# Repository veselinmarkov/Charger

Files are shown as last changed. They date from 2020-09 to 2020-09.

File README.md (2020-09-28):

# Charger
High power electric car charger

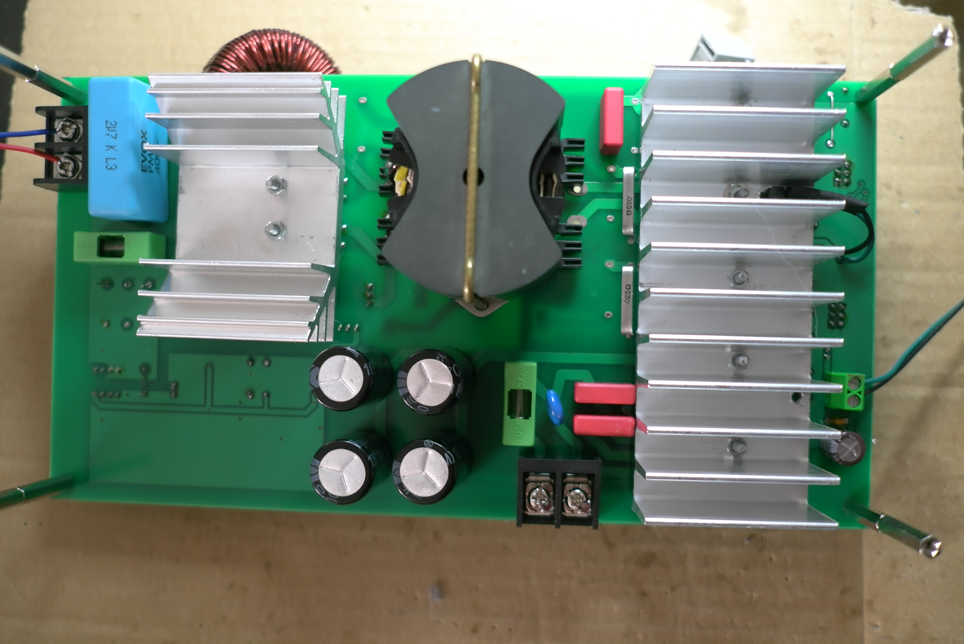
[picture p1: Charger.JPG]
Prototype board Prototype Board


The AC-DC charger was designed as part of an electric car project. 
The planned power is up to 3KW for charging 160V - 200V car batteries at nominal current of 10A, 15A at maximum. The switching frequency is 100kHz.
Apart from the core switching circuit there are some additional modules implemented, like input/output voltage measurement, overcurrent switch transistor protection, switching transistors temperature protection, CAN communication 

In the current state of the project the prototype is built, all the modules are tested and are working properly, except CAN. 
There are some topics that must be improved in to-do list

The detailed description and the first tests are collected in the Charger description document.

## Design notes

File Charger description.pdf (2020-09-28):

## Battery charger description

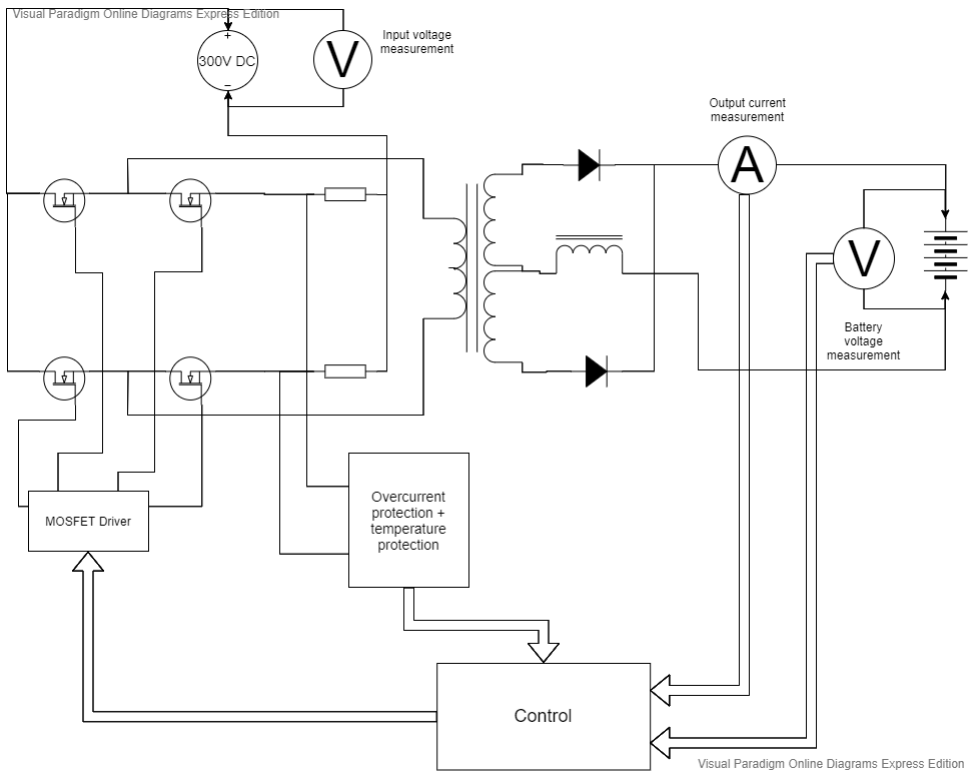
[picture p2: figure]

The charger is powered by the single phase 220V source and after rectification and filtering the DC voltage is approximately 300V. The filter capacitors need not to be large, since some pulsation is tolerable when charging batteries.

The switching type is full bridge, using phase shift technique. Both parts of the bridge are fed with fixed 50% duty cycle pulse train. The phase shift between the half bridges controls the output current. The MOSFET drive signals, current feedback and the UART control are managed by dsPIC33FJ16GS502 microcontroller. It is a special purpose PIC series for implementing in DC-DC conversions up to 400кHz.

### Switching circuit

The switching transistors are SPW17N80C3 in TO247 package. The maximum ratings are 17A drain current and 800V drain-source voltage. During the switching off phase It is highly possible to have 600V DC voltage at the transistors.

### Transformer

The transformer uses Epcos PM62/49 B65684A0000R027 ferrite N27 cores. The cores could be purchased with the matching coil former. The ratio is 12:10:10 windings with 3mm copper wire. The secondary winding is center tapped.
The transformer ratio could be changed in accordance with the battery voltage. In that case the output voltage control must be corrected in the software.

### Rectifiers

The full wave rectifier uses 2 diodes of type DSEP29-12A It is Fast Diode, 1.2 kV, 30 A, 40 ns. Have in mind that

the double voltage is applied over the reverse polarized diode in the full wave rectifier. That is why we should pick at least 1.2kV diode. It must be also soft recovery diode to decrease the switching spikes in the secondary circuit.

Filter inductor is used to limit the current in the output. I chose Epcos B66387G0000X187 ferrite with 70 wounds of 2mm wire. 1mm gap in the ferrite is required to prevent saturation at 10A charging current.

### Overcurrent and temperature protection

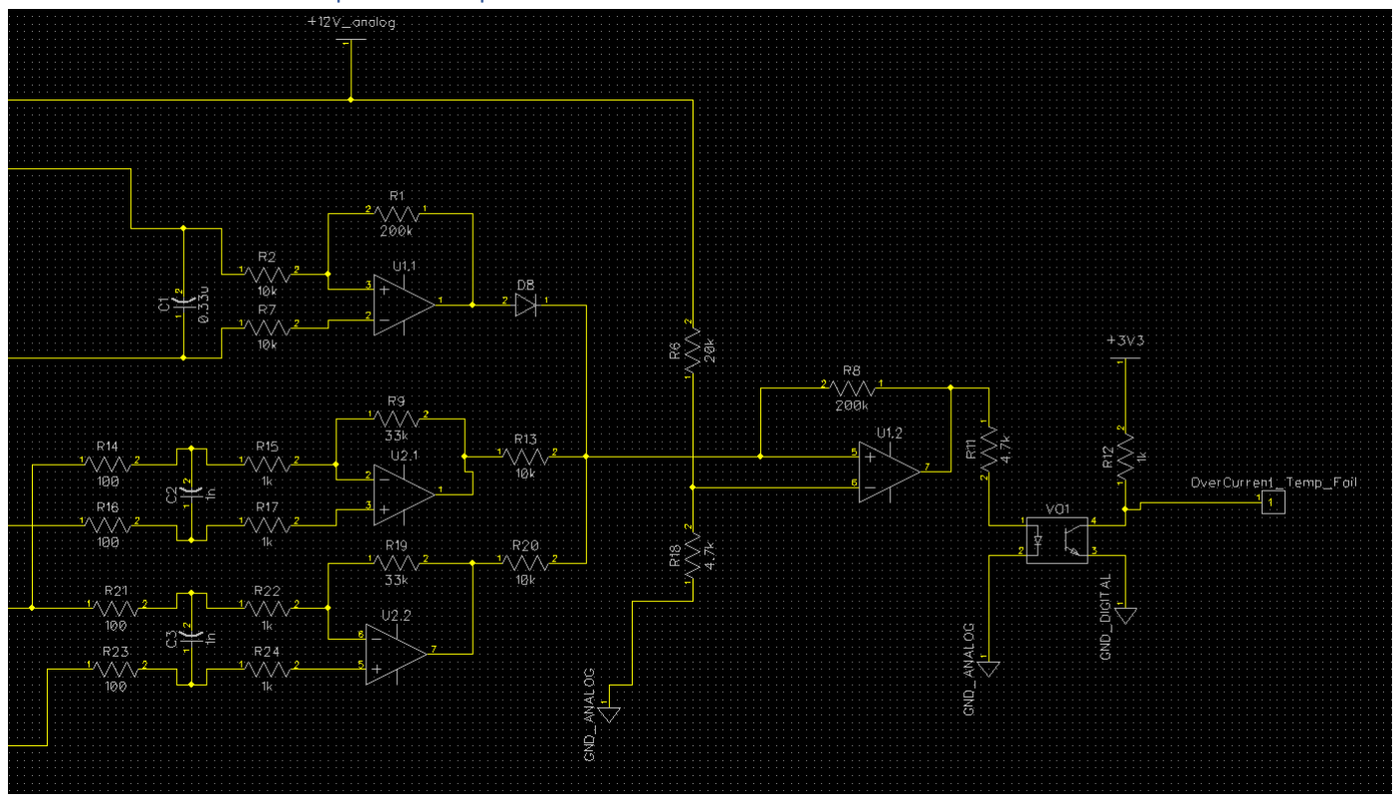
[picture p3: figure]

The overcurrent protection is accomplished of 2 shunts R1 and R2, on each leg of the bridge. After filtering the current signal is applied to the differential amplifiers U2.1 and U2.2. Adding both amplified signals goes to the comparator U1.2. In case the current via switching transistors increases above 8-9A, the overcurrent signal is triggered at pin AN2/RA2 of the PIC. The microcontroller fail-signal switches off the PWM generator. After the overcurrent condition subside, the PWM generator resumes it’s function.

The thermo protection is accomplished by a thermistor TDK B59901D0060A040. It is not shown on the circuit diagram, but the thermistor is connected to pin J3-6 and is part of the resistor bridge R3-R4-R10. Tested at 60 deg the thermistor reaches 10kOm and triggers the comparator U1.1. Via the diode D8 the thermo protection is applied to the same fail pin of the PIC microcontroller.

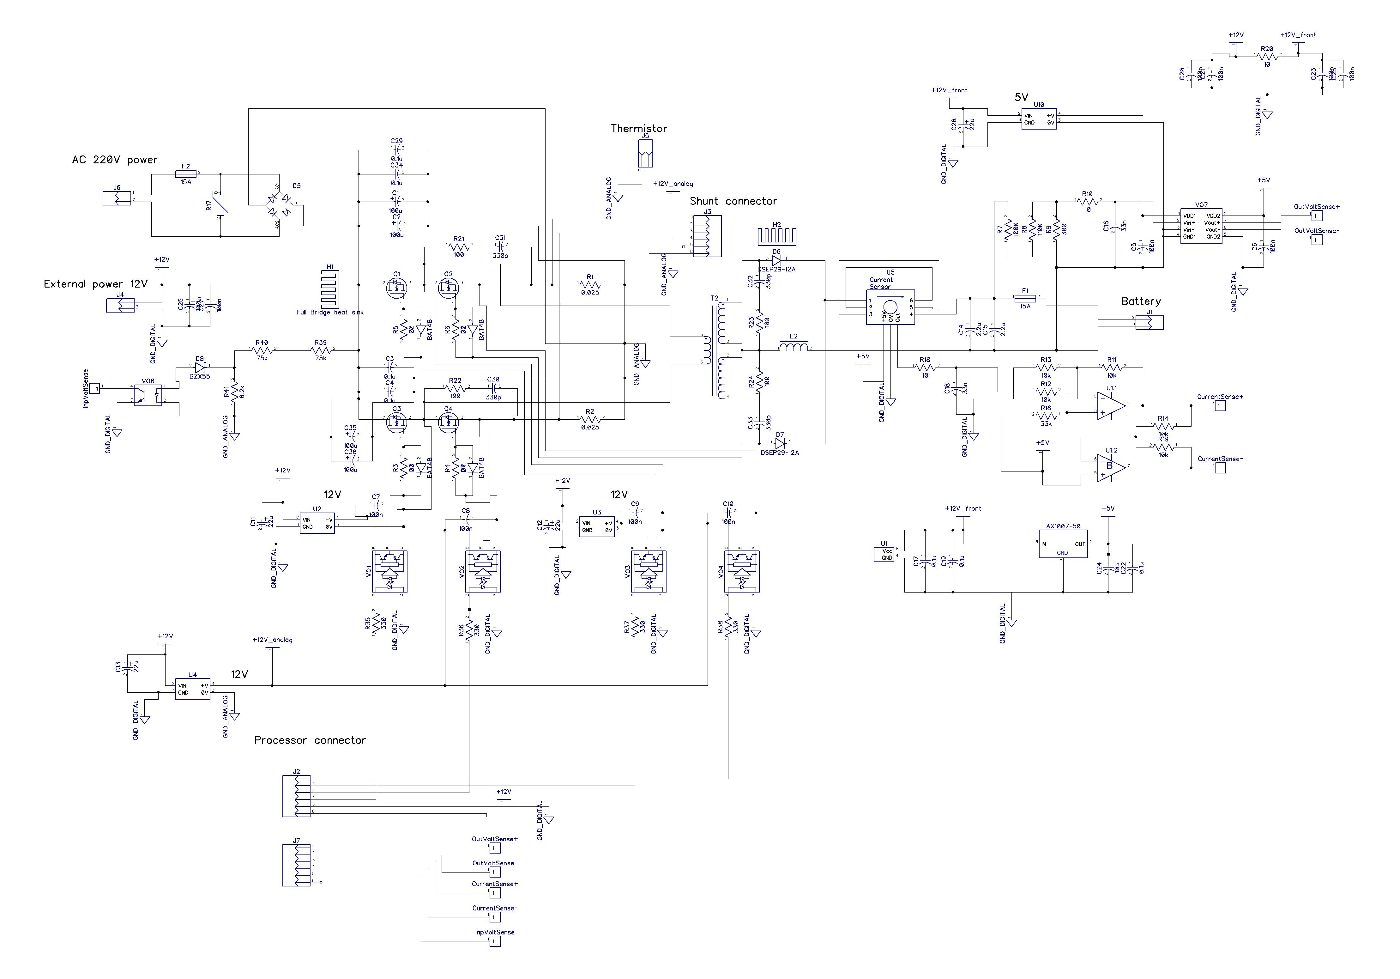
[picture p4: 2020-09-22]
Main_board_schematic.jpg

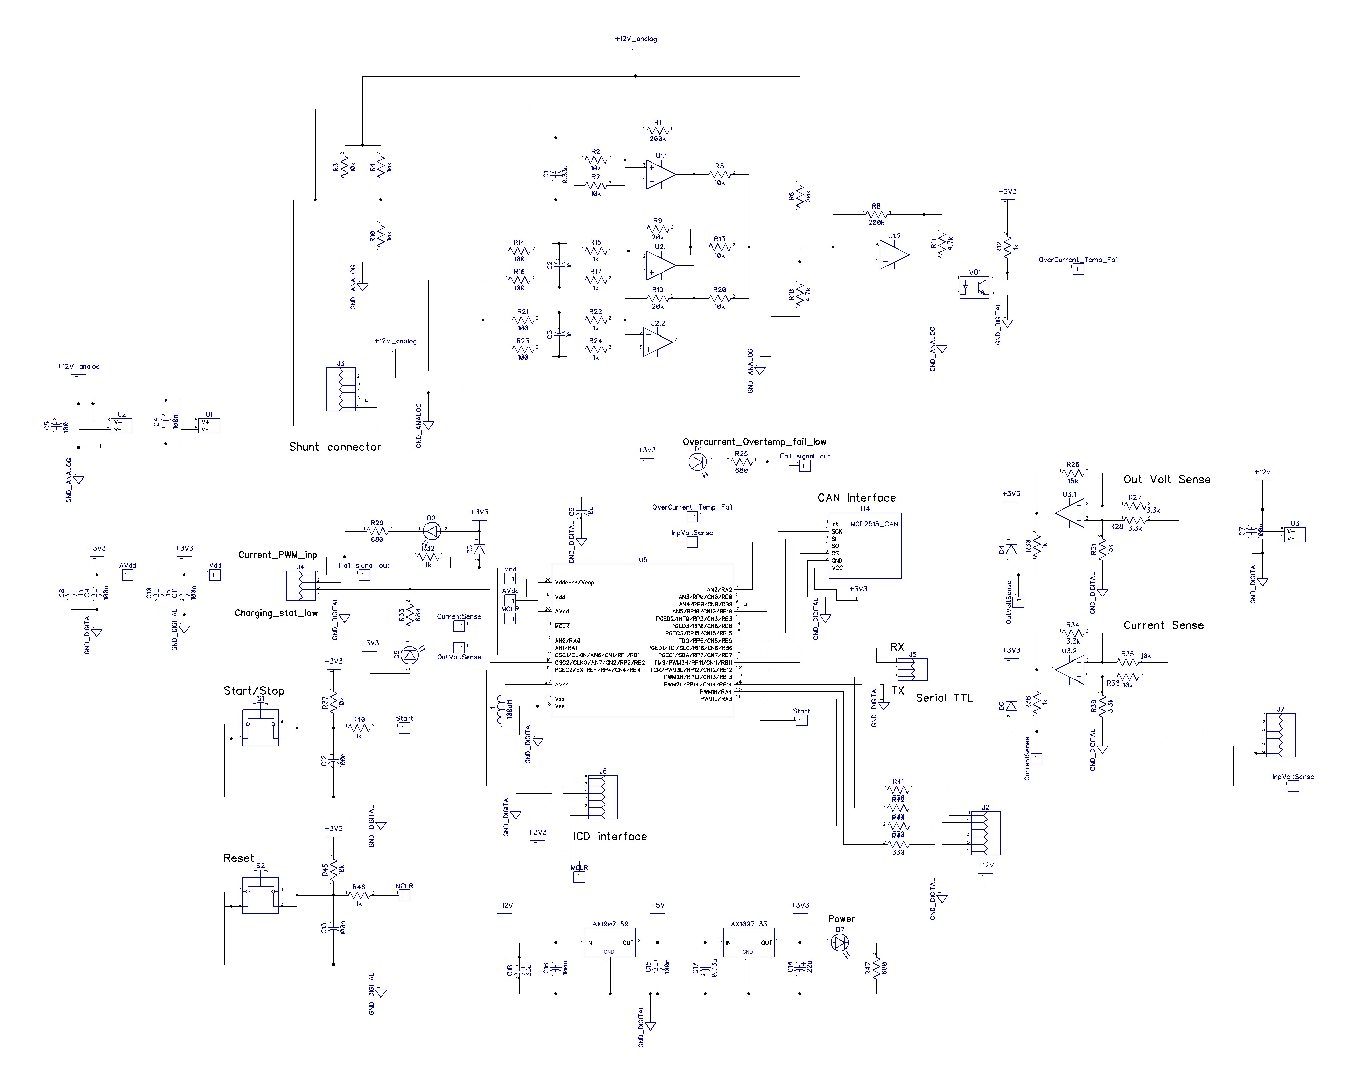
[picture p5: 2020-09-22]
Control_board_schematic.jpg

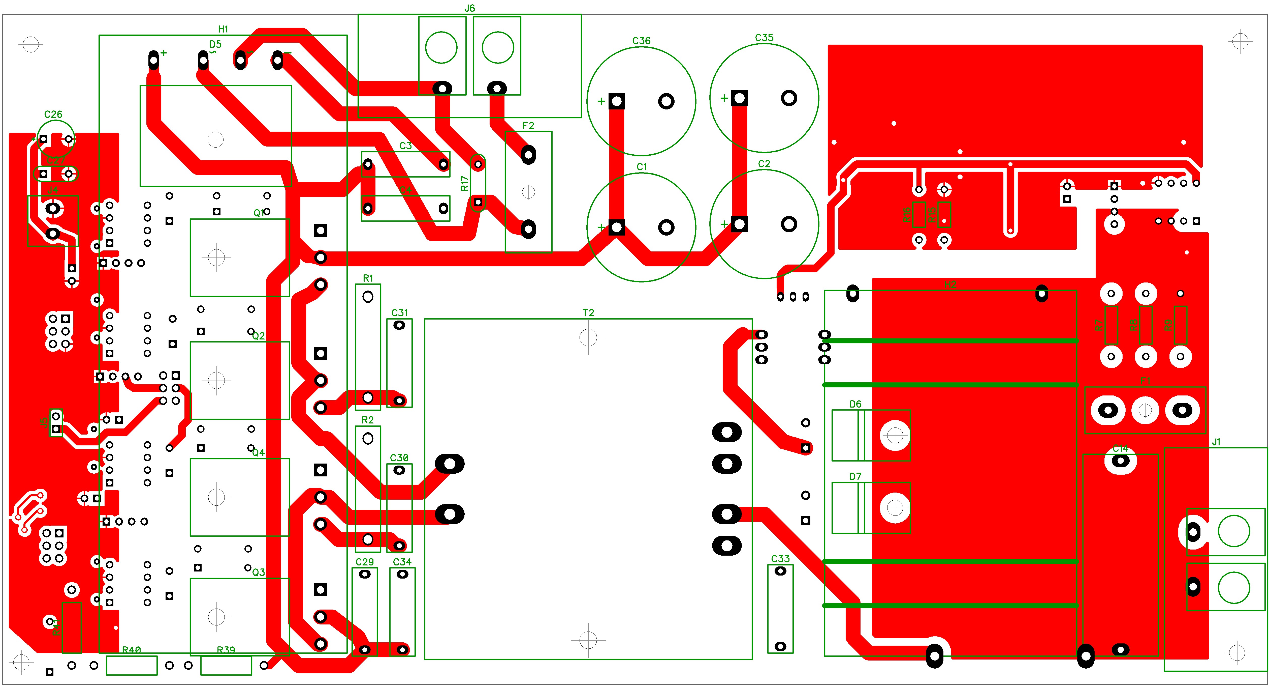
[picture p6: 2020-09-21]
pcb/Main_board_side_1.jpg

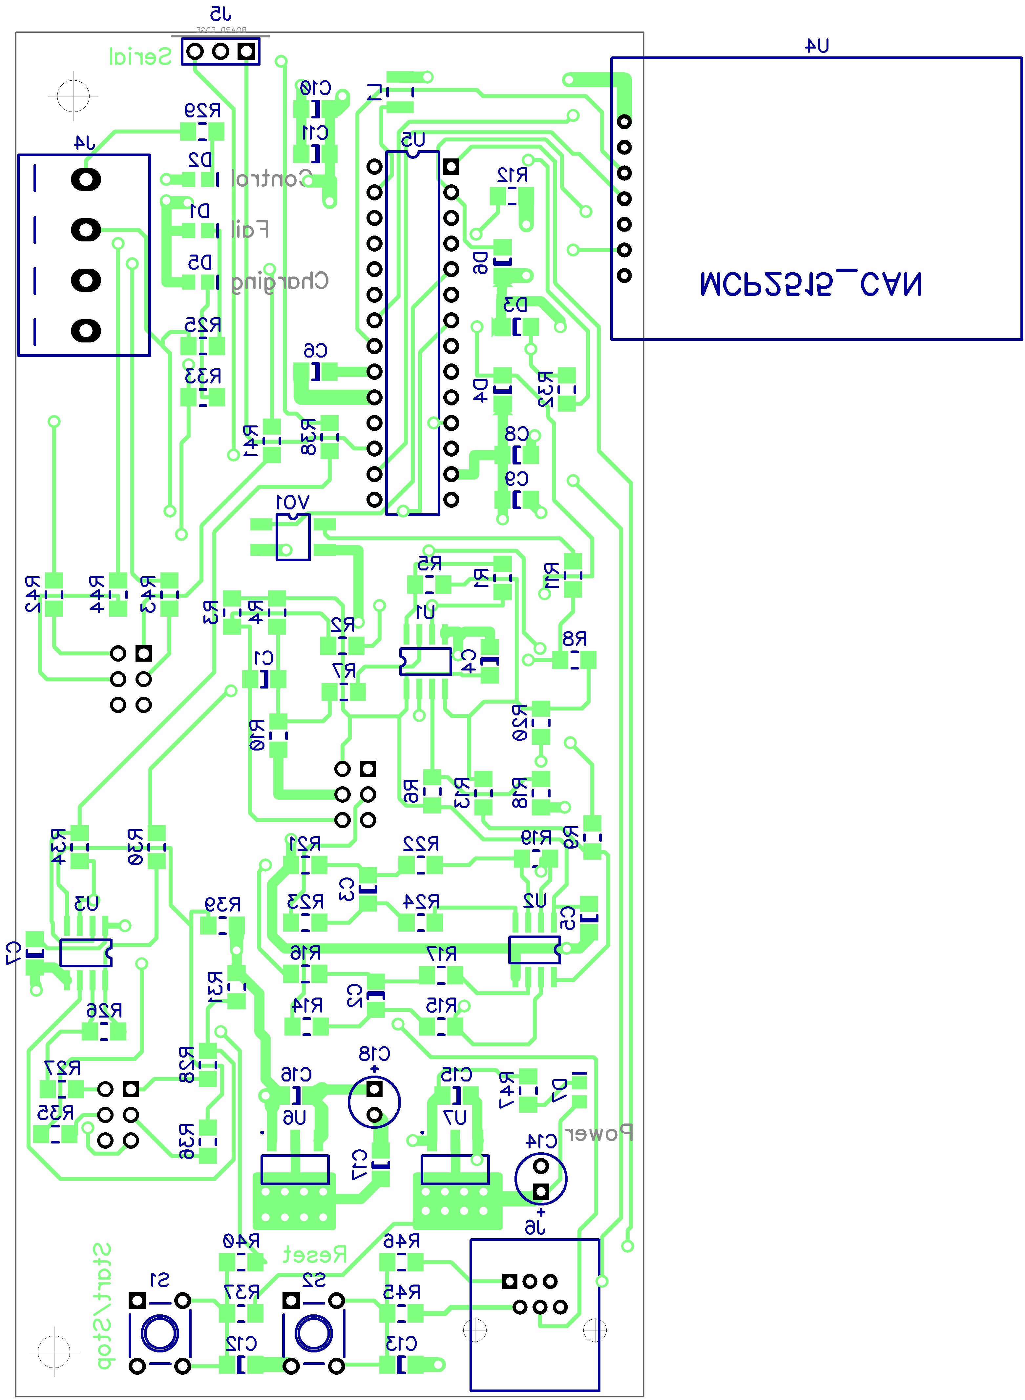
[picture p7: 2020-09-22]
pcb/Control_board_side_2.jpg

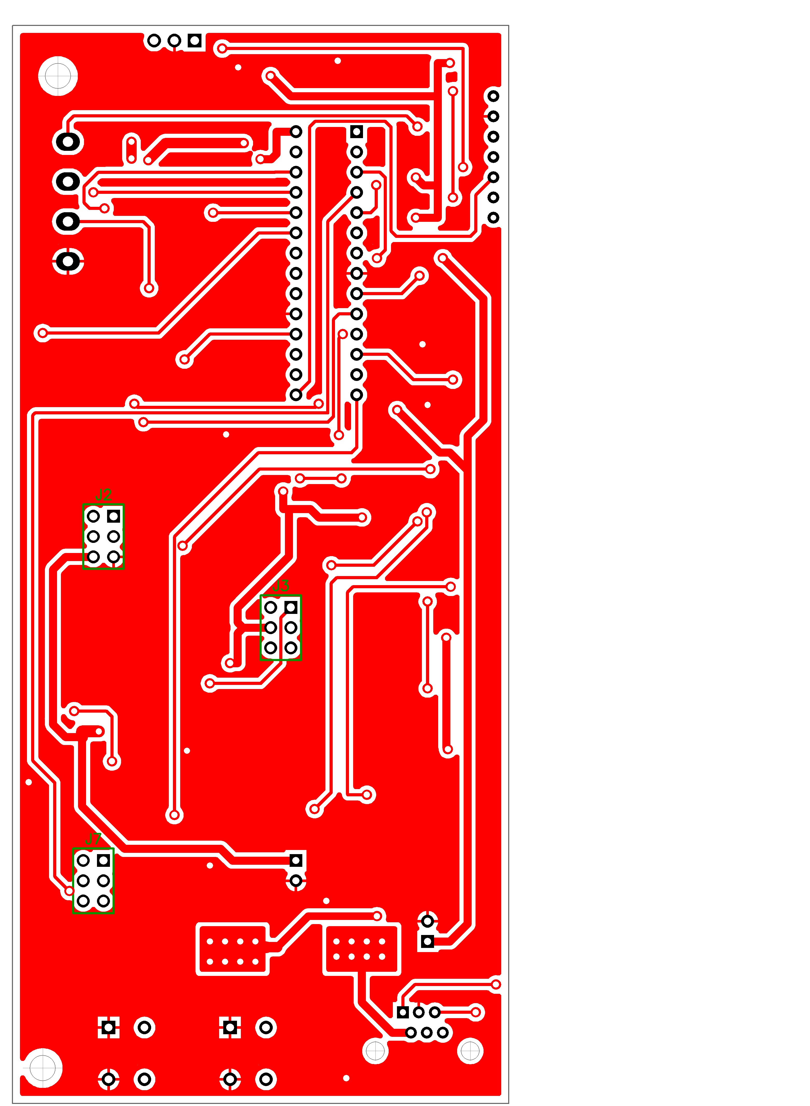
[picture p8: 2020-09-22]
pcb/Control_board_side_1.jpg

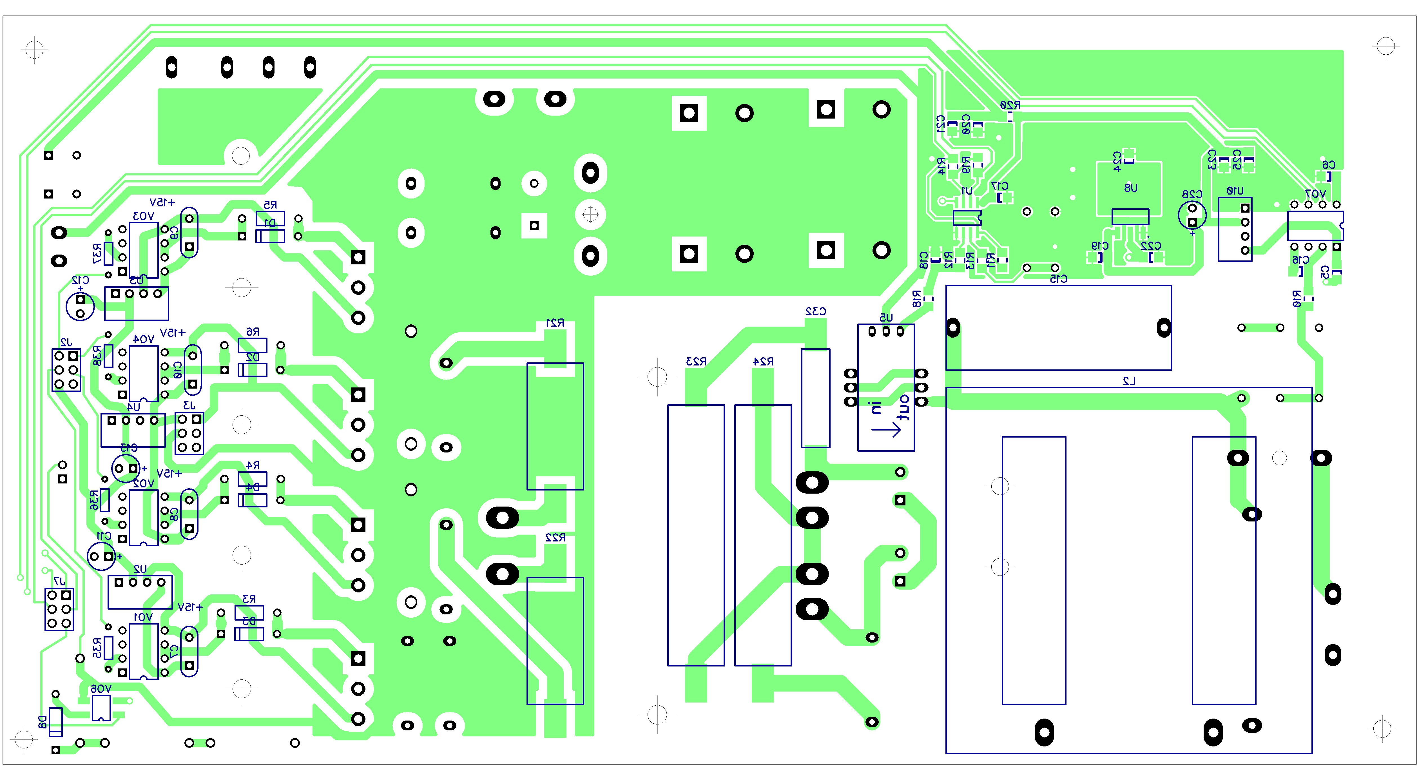
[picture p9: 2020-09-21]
pcb/Main_board_side_2.jpg

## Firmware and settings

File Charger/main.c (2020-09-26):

//Microchip example PID function is used. See their License in "pid.s" source code. The PID structure is defined in dsp.h


#include "p33FJ16GS502.h"
#include "Functions.h"
#include "CAN_transmit.h"
#include "string.h"
#include "stdio.h"
#include "stdlib.h"

_FOSCSEL(FNOSC_FRC)
_FOSC(FCKSM_CSECMD & OSCIOFNC_ON)
_FWDT(FWDTEN_OFF)
_FPOR(FPWRT_PWR128)
_FICD(ICS_PGD2 & JTAGEN_OFF)

#define OutputChargeFinish 784                                  // Not implemented: Defones voltage limit to switch off the charging

#define OutputBatteryPresent 280                                // Not implemented: Minimal voltage to detect if the battery is conncted

// extern tPID Buck1VoltagePID;
extern int zero_transducer, average, vout_average;
double AlphaOutVolt =0.0278, BetaOutVolt = 0.0;   //Alpha and Beta coefficients in the equation OutVolt =Alpha*steps +Beta for the out voltage
int PotVoltage, CurrentTarget, OutVolt1, OutVolt1steps, InVoltage, n;
char UART_logger_interval = -1;        //Return pressed via UART; if -1 the logger is switched off
extern char UART_CR;
extern char UART_buff[16];
char UART_logger_buff[150];
int PID_enable =0;
char CAN_result;

double StepToFloat(int current) {
    //return (double)0.01052*current; //95 steps per amper
    return (double)1.0 * current;
}

//current state Vout measure: R7+R8 = 3.29kOm; R9 = 33 Om; gain =1/100; max input = 30V
//              In volt=5mV; in ACPL-7900 = 1mV; out ACPL = 7mV; ADC AN1 = 50mV (noise); steps=14  
//              In volt=4.09V; in ACPL-7900 = 42mV; out ACPL = 104mV; ADC AN1 = 490mV (amp=4.54); steps =147; alpha = 0.0278
double returnOutVolt(int voltage) {
    return (double)AlphaOutVolt*voltage +BetaOutVolt;
}

void measureIdleCurrent(void) {  // PWM must be switched off before invoke
    ADCONbits.ADON = 0;
    Delay_ms(100);                                        //wait some time to measure zero current offset
    ADSTATbits.P0RDY = 0; 				  /* Clear Pair 0 data ready bit */
    ADCPC0bits.TRGSRC0 = 1;                               /* ADC Pair 0 triggered by soft trigger */
    ADCONbits.ADON = 1;                                   //enable temporary the ADC
    ADCPC0bits.SWTRG0 =1;                                 // new sample for pair 0
    while (ADSTATbits.P0RDY == 0);                         // wait to finish the zero measurement
    zero_transducer = ADCBUF0;
    ADCPC0bits.TRGSRC0 = 4; 			  /* ADC Pair 0 triggered by PWM1 */
    ADCONbits.ADON = 1;
}

int measureInputVolt(void) {
    ADSTATbits.P1RDY = 0;						// Clear the ADC pair 1 ready bit
    ADCPC0bits.SWTRG1 =1;                       // new sample for pair 1
    while (ADSTATbits.P1RDY == 0);                         // wait to finish the zero measurement
    return ADCBUF2;
 }

// Pins definitions
//Current Buck1 - AN0/RA0 (pin2) = FB0 
//Volt Buck1 out - AN1/RA1 (pin3) = FB1
//Volt Buck1 in - AN2 (pin4) = FB4
//Over current/over temp signal in - AN3/RP0/RB0 (pin5)
//Over current/over temp status active low out - AN5/RB10 (pin7)
//Charging status active low out- AN7/RB2 (pin10)
//Charging current 0-100% external drive PWM signal in - AN6/RB1 (pin9)  
//start/stop switch in - RB8/RP8 (pin14)
//SPI signals: CS - RP11 (pin21); SCK - RP12 (pin22); SI - RP5 (pin16); SO - RP15 (pin15)
//UART new: TX - RP7 (pin18) RX - RP6 (pin17)
int main(void)
{
	
	/* Configure Oscillator to operate the device at 40Mhz
	   Fosc= Fin*M/(N1*N2), Fcy=Fosc/2
 	   Fosc= 7.37*(43)/(2*2)=80Mhz for Fosc, Fcy = 40Mhz */

	/* Configure PLL prescaler, PLL postscaler, PLL divisor */
	PLLFBD = 41; 							/* M = PLLFBD + 2 */
	CLKDIVbits.PLLPOST = 0;   				/* N1 = 2 */
	CLKDIVbits.PLLPRE = 0;    				/* N2 = 2 */

    //remappable inputs
    RPINR29bits.FLT1R =0;                   // RP0/RB0 is PWM fault/current source
    TRISBbits.TRISB0 =1;                    //config RB0(RP0) as an input
    ADPCFGbits.PCFG3 =1;                    //config RP0 = AN3 AS DIGITAL/NOT ANALOG
    RPINR20bits.SDI1R =5;                   // Pin RP5 SPI:SI
    TRISBbits.TRISB5 =1;                    //config RB5(RP5) as an input
    RPINR18bits.U1RXR = 6;			// Make Pin RP6 U1RX
    TRISBbits.TRISB6 =1;                    //config RB6(RP6) as an input
    //RPINR20bits.SCK1R =12;
    //RPINR21bits.SS1R =11;
    
    //remappable outputs
    RPOR7bits.RP15R = 0b000111;  //SDO
    RPOR6bits.RP12R = 0b001000; //SCK
    RPOR5bits.RP11R = 0b001001; //CS
	RPOR3bits.RP7R = 3;		// Make Pin RB7 (RP7) U1TX
//	RPOR4bits.RP9R = 3;		// Make Pin RB9 (RP9) U1TX
    TRISBbits.TRISB15 =0;
    TRISBbits.TRISB12 =0;
    TRISBbits.TRISB11 =0;
    TRISBbits.TRISB10 =0;           //Digital out fault indication signal  AN5/RB10 (pin7)
    ADPCFGbits.PCFG5 =1;            //config  AN5/RB10 (pin7) AS DIGITAL/NOT ANALOG
    LATBbits.LATB10 =1;             //switch if off
    TRISBbits.TRISB2 =0;           //Digital out signal charging indication AN7/RB2 (pin10)
    ADPCFGbits.PCFG7 =1;            //config AN7/RB2 (pin10) AS DIGITAL/NOT ANALOG
    LATBbits.LATB2 =1;             //switch if off             

    __builtin_write_OSCCONH(0x01);			/* New Oscillator selection FRC w/ PLL */
    __builtin_write_OSCCONL(0x01);  		/* Enable Switch */
      
	while(OSCCONbits.COSC != 0b001);		/* Wait for Oscillator to switch to FRC w/ PLL */  
        while(OSCCONbits.LOCK != 1);			/* Wait for Pll to Lock */

	/* Now setup the ADC and PWM clock for 120MHz
	   ((FRC * 16) / APSTSCLR ) = (7.37MHz * 16) / 1 = 117.9MHz*/
	
	ACLKCONbits.FRCSEL = 1;					/* FRC provides input for Auxiliary PLL (x16) */
	ACLKCONbits.SELACLK = 1;				/* Auxiliary Ocillator provides clock source for PWM & ADC */
	ACLKCONbits.APSTSCLR = 7;				/* Divide Auxiliary clock by 1 */
	ACLKCONbits.ENAPLL = 1;					/* Enable Auxiliary PLL */
	
	while(ACLKCONbits.APLLCK != 1);			/* Wait for Auxiliary PLL to Lock */

    Buck1Drive();							/* PWM Setup */
        /* Complementary mode, 400kHz, dead time 25ns, ALT dt 50ns, primary timebase, disable immediate updates, trigger every cycle, fault disabled */
    CurrentandVoltageMeasurements();		/* ADC Setup */
    measureIdleCurrent();                   // Measure the Idle current and store in zero_transducer
    Buck1VoltageLoop();    					/* Initialize Buck1 PID */

    SPI_setup();
    UART_setup();
    
    IEC0bits.U1RXIE =1;                                         // Enable UART RX interrupt
    IFS0bits.U1RXIF = 0;                                        // Clear UART RX interrupt
    ADCONbits.ADON = 1;						/* Enable the ADC */
    PTCONbits.PTEN = 1;						/* Enable the PWM */
    
    //Stop the PWM
    IOCON1bits.OVRENH = 1;
    IOCON1bits.OVRENL = 1;
    IOCON2bits.OVRENH = 1;
    IOCON2bits.OVRENL = 1;

    CurrentTarget =40;              // 1Amp current target
    while(1)
    {
                    if (UART_CR ==1) {                                                       // process UART commands
                        UART_CR =0;
                        if (strncmp("ATLOGON", UART_buff, 7) ==0) {                          //start the logger
                            UART_string_out("OK");                                           
                            UART_logger_interval =0;
                        }
                        else if (strncmp("ATLOGOFF", UART_buff, 8) ==0) {                    //stop the logger                                                  // process UART commands
                            UART_string_out("OK");
                            UART_logger_interval =-1;
                        }
                        else if (strncmp("ATON", UART_buff, 4) ==0) { 
                            n =atoi(UART_buff +4);
                            if (strlen(UART_buff) ==4)
                                n = 2;
                            if (n >0) {
                                IEC6bits.ADCP0IE = 1;
                                average =0;
                                vout_average =0;                       //start the charging process
                                UART_string_out("Measurements active");
                            }
                            if (n >1) {                                            /* Enable the ADC Pair 0 interrupt current measurement*/
                                IOCON1bits.OVRENH = 0;                                           //Start the PWM
                                IOCON1bits.OVRENL = 0;
                                IOCON2bits.OVRENH = 0;
                                IOCON2bits.OVRENL = 0;                       //start the charging process
                                UART_string_out("PWM output active");
                            }
                            if (n >2) {
                                PID_enable = 1;
//                              Buck1SoftStartRoutine(5*PotVoltage);                           /* Initiate Buck 1 soft start to 5V */
                                Buck1SoftStartRoutine(CurrentTarget *32);                       //start the charging process
                                UART_string_out("PID activated");
                            }
                        }
                        else if (strncmp("ATOFF", UART_buff, 5) ==0) {              //stop the charging                                                  
                            UART_string_out("OK");
                            IEC6bits.ADCP0IE = 0;                                            /* Disable the ADC Pair 0 interrupt current measurement*/
                            IOCON1bits.OVRENH = 1;                                           //Stop the PWM
                            IOCON1bits.OVRENL = 1;
                            IOCON2bits.OVRENH = 1;
                            IOCON2bits.OVRENL = 1;
                            average =0;
                            vout_average =0;
                            UpdateControlReference(0);
                        }
                        else if (strncmp("ATCURR", UART_buff, 6) ==0) {                          //set or query current target value
                            if (strlen(UART_buff) ==6) {
                                sprintf(UART_logger_buff, "Current target: %d", CurrentTarget);
                                UART_string_out(UART_logger_buff);
                            } else {
                                n =atoi(UART_buff +6);
                                if (n >0) {
                                    CurrentTarget =n;
                                    UpdateControlReference(n *32);
                                    sprintf(UART_logger_buff, "New current target set: %d", n);
                                    UART_string_out(UART_logger_buff);
                                } else {
                                    sprintf(UART_logger_buff, "Not correct value: %s", UART_buff +6);
                                    UART_string_out(UART_logger_buff);
                                }
                            }
                        }
                        else if (strncmp("ATDTR", UART_buff, 5) ==0) {                          //set or query DTR
                            if (strlen(UART_buff) ==5) {
                                sprintf(UART_logger_buff, "DTR: %d", DTR1);
                                UART_string_out(UART_logger_buff);
                            } else {
                                n =atoi(UART_buff +5);
                                if (n >0) {
                                    UpdateDTR(n);
                                    sprintf(UART_logger_buff, "New DTR set: %d", n);
                                    UART_string_out(UART_logger_buff);
                                } else {
                                    sprintf(UART_logger_buff, "Not correct value: %s", UART_buff +5);
                                    UART_string_out(UART_logger_buff);
                                }
                            }
                        }
                        else if (strncmp("ATTRG", UART_buff, 5) ==0) {                          //set or query ADC Trigger
                            if (strlen(UART_buff) ==5) {
                                sprintf(UART_logger_buff, "Trigger: %d", TRIG1);
                                UART_string_out(UART_logger_buff);
                            } else {
                                n =atoi(UART_buff +5);
                                if (n >0) {
                                    updateTrigPeriodPercentage(n);
                                    sprintf(UART_logger_buff, "New Trigger percent set: %d", n);
                                    UART_string_out(UART_logger_buff);
                                } else {
                                    sprintf(UART_logger_buff, "Not correct value: %s", UART_buff +5);
                                    UART_string_out(UART_logger_buff);
                                }
                            }
                        }
                        else if (strncmp("ATPWM", UART_buff, 5) ==0) {                          //set or query ADC Trigger
                            if (strlen(UART_buff) ==5) {
                                sprintf(UART_logger_buff, "PWM value %d", PHASE2);
                                UART_string_out(UART_logger_buff);
                                sprintf(UART_logger_buff, "PID state: %d", PID_enable);
                                UART_string_out(UART_logger_buff);
                            } else {
                                n =atoi(UART_buff +5);
                                if (n >0) {
                                    PID_enable = 0;
                                    PHASE2 = n;
                                    sprintf(UART_logger_buff, "PID disabled. New PHASE2 value set: %d", n);
                                    UART_string_out(UART_logger_buff);
                                } else {
                                    sprintf(UART_logger_buff, "Not correct value: %s", UART_buff +5);
                                    UART_string_out(UART_logger_buff);
                                }
                            }
                        }
                        else if (strncmp("ATCALIB", UART_buff, 7) ==0) {                       //calibrate zero current
                            if (IOCON1bits.OVRENH ==0) {
                                UART_string_out("Error. Switch the charging off first");
                                continue;
                            }
                            measureIdleCurrent();
                            sprintf(UART_logger_buff, "Zero current calibrated: %d\n", zero_transducer);
                            UART_string_out(UART_logger_buff);
                        }
                        else if (strncmp("ATVO1CAL", UART_buff, 8) ==0) {                       //calibrate output voltage step1
                            n =atoi(UART_buff +8);
                            if (n >0) {
                                OutVolt1 =n;
                                OutVolt1steps =ADCBUF1;
                                if (OutVolt1steps ==0) {
                                    sprintf(UART_logger_buff, "No out voltage detected. Please connect a battery");
                                    UART_string_out(UART_logger_buff);
                                    continue;
                                }
                                AlphaOutVolt =(double)OutVolt1 /OutVolt1steps;
                                BetaOutVolt =0.0;
                                sprintf(UART_logger_buff, "Please use ATVO2CAL to improve the precision");
                                UART_string_out(UART_logger_buff);
                            } else {
                                sprintf(UART_logger_buff, "Not correct value for voltage (ATVO1CAL[1 - 999]): %s", UART_buff +8);
                                UART_string_out(UART_logger_buff);
                            }
                        }
                        else if (strncmp("ATVO2CAL", UART_buff, 8) ==0) {                       //calibrate output voltage step2
                            if (OutVolt1 ==0 || OutVolt1steps ==0) {
                                sprintf(UART_logger_buff, "Please issue ATVO1CAL first");
                                UART_string_out(UART_logger_buff);
                                continue;
                            }
                            n =atoi(UART_buff +8);
                            if (n >0) {
                                AlphaOutVolt =(double)(n -OutVolt1) /(ADCBUF1 -OutVolt1steps);
                                BetaOutVolt =OutVolt1 -AlphaOutVolt*OutVolt1steps;
                                sprintf(UART_logger_buff, "Second step completed for better volt precision");
                                UART_string_out(UART_logger_buff);
                            } else {
                                sprintf(UART_logger_buff, "Not correct value for voltage (ATVO2CAL[1 - 999): %s", UART_buff +8);
                                UART_string_out(UART_logger_buff);
                            }
                        }
                    }

                    if (UART_logger_interval >=0) {
                        UART_logger_interval++;
                        if (UART_logger_interval >10) {                                   //output current +voltages +temp
                            UART_logger_interval =0;
            //                UART_logger_buff[0] =0;
                            InVoltage = measureInputVolt();
                            sprintf(UART_logger_buff, "Out current: %.2fA; Current target: %.2fA; Zero calibrate: %d; Out voltage: %.2fV; In voltage: %d steps\n", StepToFloat(average/32), StepToFloat(CurrentTarget), zero_transducer, returnOutVolt(vout_average/32), InVoltage);
                            UART_string_out(UART_logger_buff);
                        }
                    }

                    if (U1STAbits.OERR ==1) {
                        U1STAbits.OERR =0;
                    }

                    if (!(PORTBbits.RB8) )  //&& (OutVoltage >= OutputBatteryPresent) && (OutVoltage <= OutputChargeFinish)) /* if input voltage is less than  ChargeFinish or greater than BatteryPresent then activate the PWM output */
                    {
                            PID_enable =1; 
                            IOCON1bits.OVRENH = 0;			//Start the PWM
                            IOCON1bits.OVRENL = 0;
                            IOCON2bits.OVRENH = 0;
                            IOCON2bits.OVRENL = 0;
                            IEC6bits.ADCP0IE = 1;
                            average =0;
                            vout_average =0;
                            Buck1SoftStartRoutine(CurrentTarget *32);
                            CAN_result =CAN_read(CANCTRL);
                    }
                    

                    //for CAN mcp2515 to transmit data must load al least TXBnDLC-data lenght code, TXB0SIDH-standard dientifier high, TXB0SIDL-SID low

                    /*
                    if ((OutVoltage < OutputBatteryPresent) || (OutVoltage > OutputChargeFinish)) // if input voltage is less than
                                                    BatteryPresent (no battery connected) or greater than ChargeFinish then deactivate the PWM output 
                    {
                            IOCON1bits.OVRENH = 1;			//Stop the PWM
                            IOCON1bits.OVRENL = 1;
                    }
                     */
					//        LATBbits.LATB12 =~PORTBbits.RB8;    //Indicate PWM cycle start
                    Delay_ms(200);          //delay the main loop at 0.5 s. intervals
                    LATBbits.LATB10 = PORTBbits.RB0;    //indicate overcurrent/temperature fault LED
                    PID_enable = PORTBbits.RB0; //switch on/off PID when overcurrent/temperature fault
                    //LATBbits.LATB10 =1;     //Reset the overcurrent/temp fail out
                    LATBbits.LATB2 = IOCON1bits.OVRENH;     //indicate the charging status LED
    }

}

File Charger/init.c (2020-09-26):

#include "p33FJ16GS502.h"
#include "Functions.h"
#include "dsp.h"
#include "CAN_transmit.h"

/* Variable Declaration required for each PID controller in the application. */
tPID Buck1VoltagePID; 

/* These data structures contain a pointer to derived coefficients in X-space and 
   pointer to controler state (history) samples in Y-space. So declare variables 
   for the derived coefficients and the controller history samples */
fractional Buck1VoltageABC[3] __attribute__ ((section (".xbss, bss, xmemory")));
fractional Buck1VoltageHistory[3] __attribute__ ((section (".ybss, bss, ymemory")));

#define PID_BUCK1_KP 0.23
#define PID_BUCK1_KI 0.0016
#define PID_BUCK1_KD 0

/* These macros are used for faster calculation in the PID routine and are used for limiting the PID Coefficients */
#define PID_BUCK1_A Q15(PID_BUCK1_KP + PID_BUCK1_KI + PID_BUCK1_KD) //A = 0.2316
#define PID_BUCK1_B Q15(-1 *(PID_BUCK1_KP + 2 * PID_BUCK1_KD))      //B = -0.23
#define PID_BUCK1_C Q15(PID_BUCK1_KD)                               //C = 0

#define TRIG_OFFSET             140      // small offset for the ADC trigger

/* This is increment rate to give us the sofstart */
 #define BUCK1_SOFTSTART_INCREMENT	 40

int zero_transducer, average, vout_average;       //zero value; running average of the measured current
extern unsigned int TimerInterruptCount;
char CAN_stat_result;

void SPI_setup(void)
{
    //__builtin_write_OSCCONL(0x46);
    //__builtin_write_OSCCONH(0x57);
    //OSCCONbits.IOLOCK =0; // enable changing RPIN and RPOR registers
 
    //__builtin_write_OSCCONL(0x46);
    //__builtin_write_OSCCONH(0x57);
    //OSCCONbits.IOLOCK =1; // prevent changing RPIN and RPOR registers

    //Prescalers: in case Fck =40MHz, the baud rate is 104.17KHz
    SPI1CON1bits.PPRE =0b00;    //64:1
    SPI1CON1bits.SPRE =0b010;   //6:1
    
    //setup the SPI1
    IFS0bits.SPI1IF = 0; //Clear the Interrupt Flag
    IEC0bits.SPI1IE = 0; //disable the Interrupt
    SPI1CON1bits.DISSCK = 0; //Internal Serial Clock is Enabled.
    SPI1CON1bits.DISSDO = 0; //SDOx pin is controlled by the module.
    SPI1CON1bits.MODE16 = 0; //Communication is word-wide (16 bits).
    SPI1CON1bits.SMP = 0; //Input Data is sampled at the middle of data output time.
    SPI1CON1bits.CKE = 1; //Serial output data changes on transition from
                           //Idle clock state to active clock state
    SPI1CON1bits.CKP = 0; //Idle state for clock is a low level;
                        //active state is a high level
    SPI1CON1bits.MSTEN = 1; //Master Mode Enabled
    SPI1STATbits.SPIEN = 1; //Enable SPI Module

    Delay_ms(1);
    //issue reset command
    CAN_reset();
    Delay_ms(1);

    CAN_write(CANCTRL, 0b00001110); // clock/4; clock out pin enabled; one-shot mode; set normal operation mode
    CAN_stat_result =CAN_read(CANSTAT);
}

void UART_setup(void) {
    #define FCY             39613000        //Instruction Cycle Frequency
    #define BAUDRATE         9600
    #define BRGVAL          ((FCY/BAUDRATE)/16)-1 // calculate UART prescaler value
    U1BRG  = BRGVAL;
    U1MODEbits.UARTEN = 1; /* Reset UART to 8-n-1, alt pins, and enable */
    U1STAbits.UTXEN  = 1; /* Reset status register and enable TX & RX*/
//    U1MODEbits.ABAUD =1;
}

void Buck1Drive(void)
{
    #define PERIOD 4800 // for 100KHz PWM period
    PTCON2bits.PCLKDIV =1;                  //master PWM clock divider; changes the PWM freq. from 200kHz to 100kHz period
    PTPER = PERIOD;

//  PWM#1
    IOCON1bits.PENH = 1;                  /* PWM1H is controlled by PWM module */
    IOCON1bits.PENL = 1;                  /* PWM1L is controlled by PWM module */

    IOCON1bits.PMOD = 0;                  /* Complementary Mode */
    
    IOCON1bits.POLH = 0;                  /* Drive signals are active-high */
    IOCON1bits.POLL = 0;                  /* Drive signals are active-high */

    IOCON1bits.OVRENH = 0;				  /* Disable Override feature for shutdown PWM */
    IOCON1bits.OVRENL = 0;				  /* Disable Override feature for shutdown PWM */
    IOCON1bits.OVRDAT = 0b00;			  /* Shut down PWM with Over ride 0 on PWMH and PWML */

    PWMCON1bits.DTC = 0;                  /* Positive Deadtime enabled */
    
    DTR1    = 80;                        // DT is about 100ns
    ALTDTR1 = 80;                        // alt DT is about 150ns

    PWMCON1bits.IUE = 0;                  /* Disable Immediate duty cycle updates */
    PWMCON1bits.ITB = 0;                  /* Select Primary Timebase mode */
    PWMCON1bits.CLIEN = 1;                // Enable Current limit interrupt
            
    TRGCON1bits.TRGDIV = 0b1111;               /* Trigger interrupt generated every 16-th PWM cycle */
    TRGCON1bits.TRGSTRT = 0;              /* Trigger generated after waiting 0 PWM cycles */

    PDC1 = PERIOD /2;                            /* 50% Initial pulse-width = minimum deadtime required (DTR1 + ALDTR1)*/
    TRIG1 = PERIOD -TRIG_OFFSET;                            /* Trigger generated at beginning of PWM active period */

    FCLCON1bits.CLSRC = 0;                // Current source 0
    FCLCON1bits.CLPOL = 1;                // Invert current source = active low
    FCLCON1bits.CLMOD = 1;                // Enable current limiting
    FCLCON1bits.FLTMOD = 3;               /* Fault Disabled */

//  PWM#2
    IOCON2bits.PENH = 1;                  /* PWM1H is controlled by PWM module */
    IOCON2bits.PENL = 1;                  /* PWM1L is controlled by PWM module */

    IOCON2bits.PMOD = 0;                  /* Complementary Mode */

    IOCON2bits.POLH = 0;                  /* Drive signals are active-high */
    IOCON2bits.POLL = 0;                  /* Drive signals are active-high */

    IOCON2bits.OVRENH = 0;				  /* Disable Override feature for shutdown PWM */
    IOCON2bits.OVRENL = 0;				  /* Disable Override feature for shutdown PWM */
    IOCON2bits.OVRDAT = 0b00;			  /* Shut down PWM with Over ride 0 on PWMH and PWML */

    PWMCON2bits.DTC = 0;                  /* Positive Deadtime enabled */

    DTR2    = 80;                        // DT is about 100ns

    ALTDTR2 = 80;                       // alt DT is about 150ns

    PWMCON2bits.IUE = 0;                  /* Disable Immediate duty cycle updates */
    PWMCON2bits.ITB = 0;                  /* Select Primary Timebase mode */

    PDC2 =PERIOD /2;
    PHASE2 = 1200;
    
    FCLCON2bits.CLSRC = 0;                // Current source 0
    FCLCON2bits.CLPOL = 1;                // Invert current source = active low
    FCLCON2bits.CLMOD = 1;                // Enable current limiting
    FCLCON2bits.FLTMOD = 3;               /* Fault Disabled */

    IEC5bits.PWM1IE =1;                   //Enable PWM1 interrupt (capture Current limit)
}

void updateTrigPeriodPercentage(unsigned int perc) {
    TRIG1 = (double)perc/100*PERIOD;
}
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
